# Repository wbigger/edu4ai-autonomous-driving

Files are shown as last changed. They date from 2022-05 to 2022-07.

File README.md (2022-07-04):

# EDU4AI - Autonomous Driving Cars

This tutorial is part of the following EU funded project:

Edu4AI - Artificial Intelligence and Machine Learning to Foster 21st Century Skills in Secondary Education, in the framework of Erasmus+, Grant Agreement VG-IN-BY-20-25-077366

# Final result
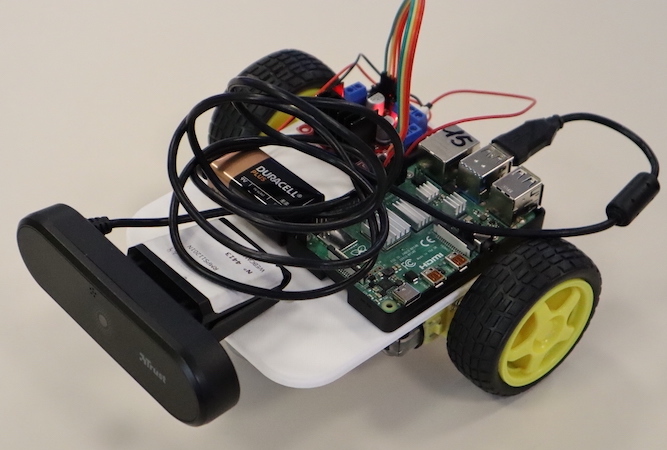
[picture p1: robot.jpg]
Robot, complete


# Get the parts
For our project we used the following parts
- [ ] Raspberry Pi version 4
- [ ] MicroSD card minimum size 16 GB
- [ ] Two wheels with rubber tires
- [ ] L298N Motor Drive Controller
- [ ] USB 5V power bank, with at least a good quality [2.5A power output](https://www.raspberrypi.com/products/raspberry-pi-4-model-b/specifications/) (USB-C)
- [ ] 9V battery with clip
- [ ] USB webcam with hole for tripod
- [ ] Jumper wires F/F and F/M, to connect everything
- [ ] M2.5 and M3 screws, assorted lengths
- [ ] double-sided tape or Patafix
- [ ] 1/4" slotted screw (for camera)
- [ ] ball castor (we used a two-holes ball castor, with distance of 38mm between them)
- [ ] a micro-HDMI to HDMI cable or adapter to connect your Raspberry to a monitor

Optional:
- [ ] Raspberry case

Just as reference, you can see the list part [here](https://www.amazon.it/hz/wishlist/ls/2XP57TFXQNB8H?ref_=wl_share).

## Chassis
More information on how we created the chassis in the [dedicated page](./chassis).

## Power
In this project, we use two separated power source:
- [ ] a power bank for the Raspberry PI
- [ ] a 9V battery for motors (rechargable)

Note: we cannot use the Raspberry Pi to power motors, since its output are not suitable for supporting loads, so we need an additional power supply, and a 9V battery is a good solution. 

We reccomend rechargable 9V batteries, since common 9V battery would last less than hours, according to our experience (see the shopping list above for details).

According to [official documentation](https://www.raspberrypi.com/products/raspberry-pi-4-model-b/specifications/), we can use a good quality 2.5A power bank to power the board if the downstream USB peripherals consume less than 500mA in total. We have only one peripheral, the webcam, that should stay inside this limit.

# L298N <-> Raspberry Pi GPIO pins

| L298N | Raspberry PI GPIO PIN | Raspberry Pi pin description |
|---|---|---|
| IN1 | 29 | GPIO5 |
| IN2 | 31 | GPIO6 |
| IN3 | 37 | GPIO26 |
| IN4 | 36 | GPIO16 |
| GND | 39 | GND |

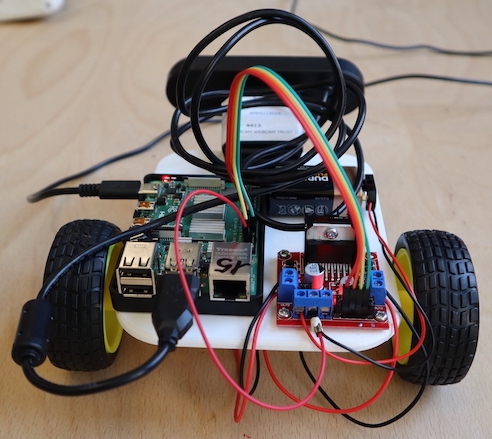
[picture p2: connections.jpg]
Robot rear with connections

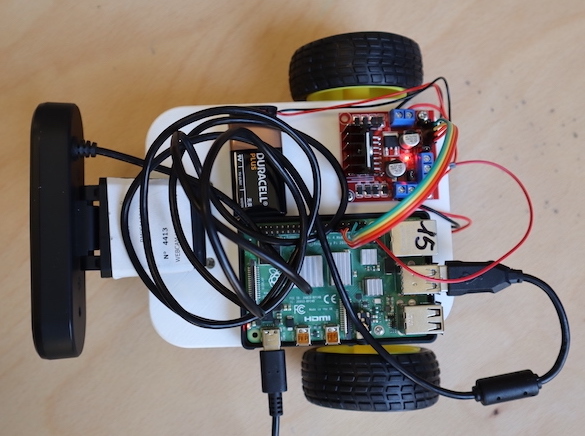
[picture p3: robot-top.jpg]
Robot top


# Prepare the SD Card
We used the official [Raspberry Pi OS](https://www.raspberrypi.com/software/operating-systems/).

We tested the project with:
- Raspberry Pi OS with desktop
- Release date: April 4th 2022
- System: 32-bit
- Kernel version: 5.15
- Debian version: 11 (bullseye)

# Set up the Raspberry Pi

Connect a mouse, keyboard and monitor to your Raspberry Pi and power it. Follow configuration and initialisation instructions if any.

To upgrade the Operating System, open a Terminal window and execute:

```sh
sudo apt update
sudo apt -y dist-upgrade
```

Answer 'yes' to any prompts.

Now we should install VNC (Virtual Network Computing) to access the Robot remotely using our Windows laptop.

Install VNC server on the Raspberry Pi

```sh
sudo apt update
sudo apt install realvnc-vnc-server
```

Then from the Pi menu enable the VNC by:
Raspberry Pi Menu->Preferences->Raspberry Pi Configuration->Interface tab->Enable VNC and click OK.

After that you should install a VNC viewer on your Windows laptop; you can download it [here](https://www.realvnc.com/en/connect/download/viewer/).

Get the IP from the Raspberry using:

```sh
hostname -I
```

Put this IP into the VNC viewer on your laptop.

# Move the motors
We are now almost ready to actually move the motors.

On the Raspberry PI, click on the menu on the top right->Programming->Thonny Python IDE.

```py
from gpiozero import Robot
myRobot = Robot(right=(26,16), left=(5,6))

# Argument is the speed, from 0 (stop) to 1 (max speed, default),
# leave empty for default.
# I suggest to start with 0.6, and eventually change it.
# Use these commands on the intearctive console.

myRobot.forward(0.6)  # go forward
myRobot.backward(0.6) # go backward
myRobot.left(0.6) # turn left
myRobot.right(0.6) # turn right
myRobot.stop() # turn right
```

# Train your model
Go to [Teachable Machine](https://teachablemachine.withgoogle.com/train).

Use "Standard Image Model"

After training, export as Tensorflow Lite -> Quantized

We used the [Duckietown Traffic Signs](https://docs.duckietown.org/daffy/opmanual_duckietown/draft/dt_ops_appearance_specifications.html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) to train the model.

# Test trained model with your car

Open a terminal on Raspberry Pi and install dependencies.

```sh
sudo apt update
sudo apt -y install libjpeg-dev libtiff5-dev libjasper-dev libpng-dev
sudo apt -y install libavcodec-dev libavformat-dev libswscale-dev libv4l-dev
sudo apt -y install libxvidcore-dev libx264-dev
sudo apt -y install libatlas-base-dev

pip3 install opencv-python

pip3 install tflite-runtime

pip3 install numpy --upgrade
```

Create a folder on Raspberry, unzip the Tensorflow model and download the [classify_webcam.py](classify_webcam.py) example inside it.

Inside a terminal, test that everything works:

```sh
python3 classify_webcam.py --model myModel/model.tflite --labels myModel/labels.txt
```

With this script, without any modification, you can immediatly check that image detection works and manually drive the robot using WASD keys. 

However, you need to modify it to actually implement an autonomous driving.

# Follow a path
To challenge students in something mesaurable, we drew a path on the floor of the laboratory with scotch tape.

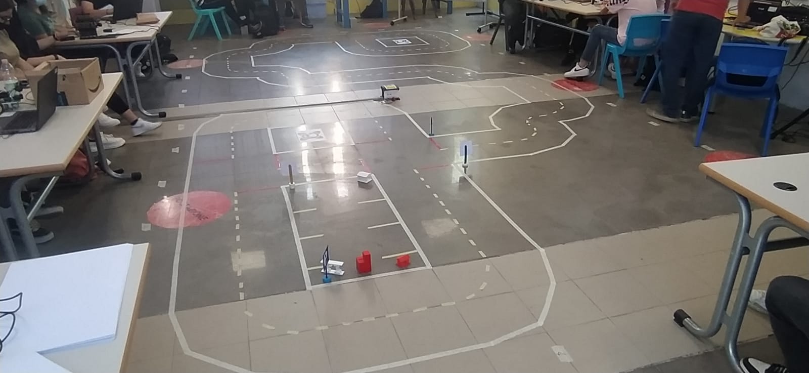
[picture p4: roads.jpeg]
Roads with scotch tape


We used [Duckietown Navigation](https://docs.rs-online.com/e1c9/A700000007310061.pdf) specification to draw the roads. This is not mandatory, since we do not want to participate in Duckietown competitions and we did not follow exactly the standard, but it is useful to have a starting point. In particular, we did not trained AI to follow the lines, but just to recognize traffic signs.

We also used [Duckietown Map-Utils](https://github.com/duckietown/map-utils) repository to generate a random map, but a simple ring in a 3x3 map should be enough to start challenging student in following a path with traffic signs.

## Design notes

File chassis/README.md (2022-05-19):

# Robot chassis

## Modeling
For the chassis, we created [this](https://cad.onshape.com/documents/15c321ccd0213a232c1b2dd5/w/b4b8e765f4b619d71b8de61f/e/8b93bb84c32f0defb354983d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) project using OnShape. OnShape is a completely online CAD, free to use for students and educators.

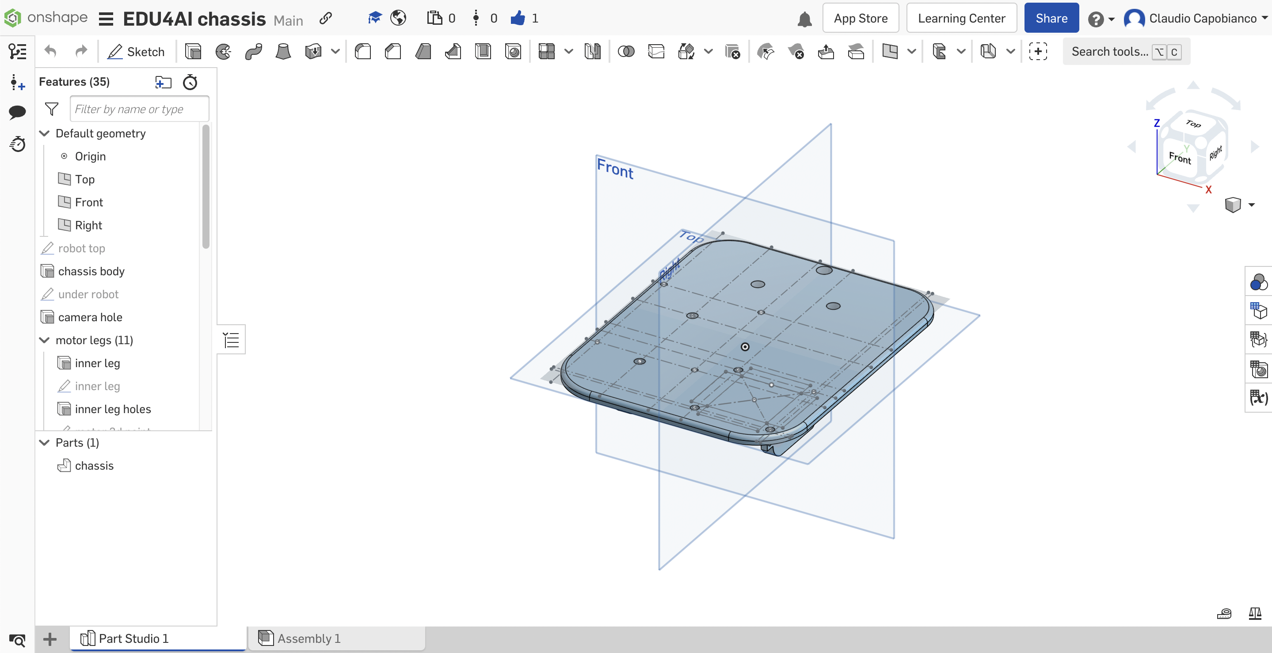
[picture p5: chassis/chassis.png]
chassis


## Printing
In this folder you can also find the [STL](./chassis-v6.stl) version of the main revisions.

We printed the chassis with common PLA.

The chassis is far to be perfect, could be largely improved. We favored simplicity for 3D printing, using a single part and a flat side to adhere to the build plate. Please feel free to modify it according to your needs.

Here you can see some of test prints and the final prints ready to be used by students!

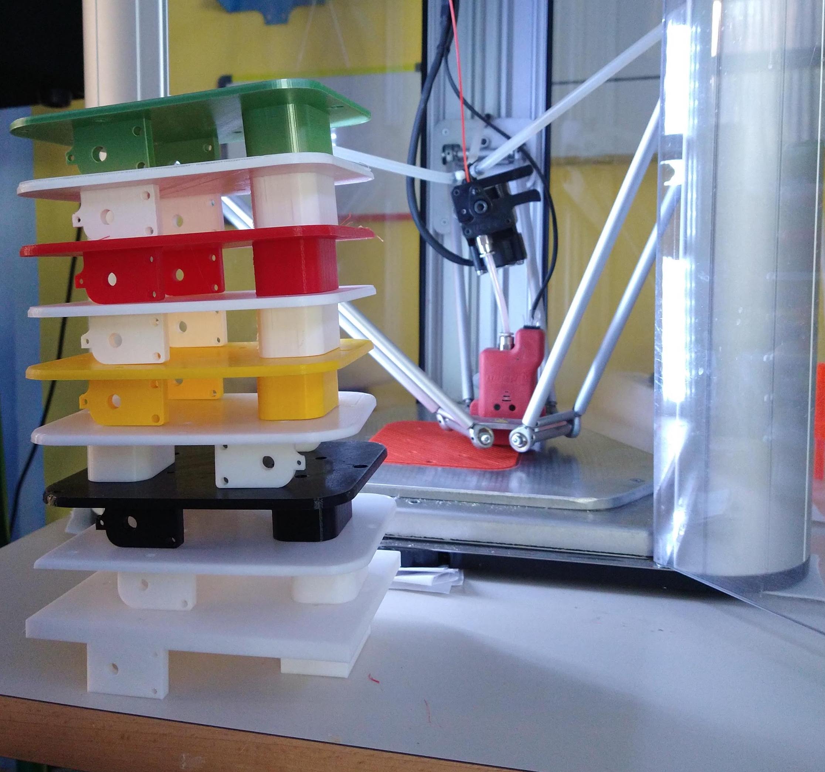
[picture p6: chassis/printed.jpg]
Printed versions


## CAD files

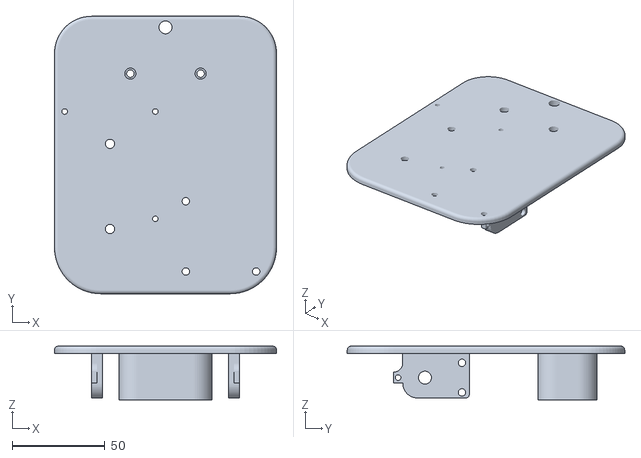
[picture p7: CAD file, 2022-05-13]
chassis/chassis-v6.stl
120.0 x 150.0 x 29.0

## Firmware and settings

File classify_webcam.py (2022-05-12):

# python3

import argparse
import time
import numpy as np

import cv2
from threading import Thread

from tflite_runtime.interpreter import Interpreter

from gpiozero import Robot

class VideoStream:
    """Camera object that controls video streaming from Picamera"""
    def __init__(self,resolution=(640,480),framerate=30):
        self.stream = cv2.VideoCapture(0)
        ret = self.stream.set(cv2.CAP_PROP_FOURCC,cv2.VideoWriter_fourcc(*'MJPG'))
        ret = self.stream.set(3,resolution[0])
        ret = self.stream.set(4,resolution[1])

        (self.grabbed, self.frame) = self.stream.read()

        self.stopped = False

    def start(self):
        Thread(target=self.update,args=()).start()
        return self

    def update(self):
        while True:
            if self.stopped:
                self.stram.release()
                return

            (self.grabbed,self.frame) = self.stream.read()

    def read(self):
        return self.frame

    def stop(self):
        self.stopped = True

def load_labels(path):
    with open(path,'r') as f:
        return {i: line.strip() for i,line in enumerate(f.readlines())}

def set_input_tensor(interpreter,image):
    tensor_index = interpreter.get_input_details()[0]['index']
    input_tensor = interpreter.tensor(tensor_index)()[0]
    input_tensor[:,:] = image

def classify_image(interpreter,image,top_k=1):
    set_input_tensor(interpreter,image)
    interpreter.invoke()
    output_details = interpreter.get_output_details()[0]
    output = np.squeeze(interpreter.get_tensor(output_details['index']))

    if output_details['dtype'] == np.uint8:
        scale, zero_point = output_details['quantization']
        output = scale * (output - zero_point)

    ordered = np.argpartition(-output,top_k)
    return [(i,output[i]) for i in ordered[:top_k]]

def main():
    parser = argparse.ArgumentParser(formatter_class = argparse.ArgumentDefaultsHelpFormatter)
    parser.add_argument('--model',help='File path of .tflite file.',required=True)
    parser.add_argument('--labels',help='File path of labels file.',required=True)
    args = parser.parse_args()

    labels = load_labels(args.labels)

    interpreter = Interpreter(args.model)
    interpreter.allocate_tensors()
    _,height,width,_ = interpreter.get_input_details()[0]['shape']

    botino = Robot(left=(5,6), right=(26,16))

    videostream = VideoStream(resolution=(640,480),framerate=30).start()
    time.sleep(1)

    while True:
        frame1 = videostream.read()

        frame = frame1.copy()
        frame_rgb = cv2.cvtColor(frame,cv2.COLOR_BGR2RGB)
        frame_resized = cv2.resize(frame_rgb, (width,height))
        input_data = np.expand_dims(frame_resized,axis=0)

        start_time = time.time()
        results = classify_image(interpreter,input_data)
        elapsed_ms = (time.time() - start_time) * 1000
        label_id,prob = results[0]

        label = '%s %.2f %.1fms' % (labels[label_id],prob, elapsed_ms)
        cv2.putText(frame,label,(5,30), cv2.FONT_HERSHEY_SIMPLEX,0.9,(0,255,0),2)

        cv2.imshow('Object detector',frame)

        key = cv2.waitKey(1)

        if key == ord('q'):
            break

        if key == ord('w'):
            botino.forward(0.8)

        if key == ord('s'):
            botino.backward(0.8)

        if key == ord('a'):
            botino.left(0.8)

        if key == ord('d'):
            botino.right(0.8)

        if key == -1:
            # KEY RELEASED
            botino.stop()

    # Clean up
    cv2.destroyAllWindows()
    videostream.stop()

if __name__ == '__main__':
    main()

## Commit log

2022-05-19 Add image to chassis page
2022-05-19 Add image with printed chassis
